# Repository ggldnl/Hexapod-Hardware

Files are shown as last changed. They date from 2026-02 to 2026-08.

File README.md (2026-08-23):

# Hexapod Hardware

<div align="center">
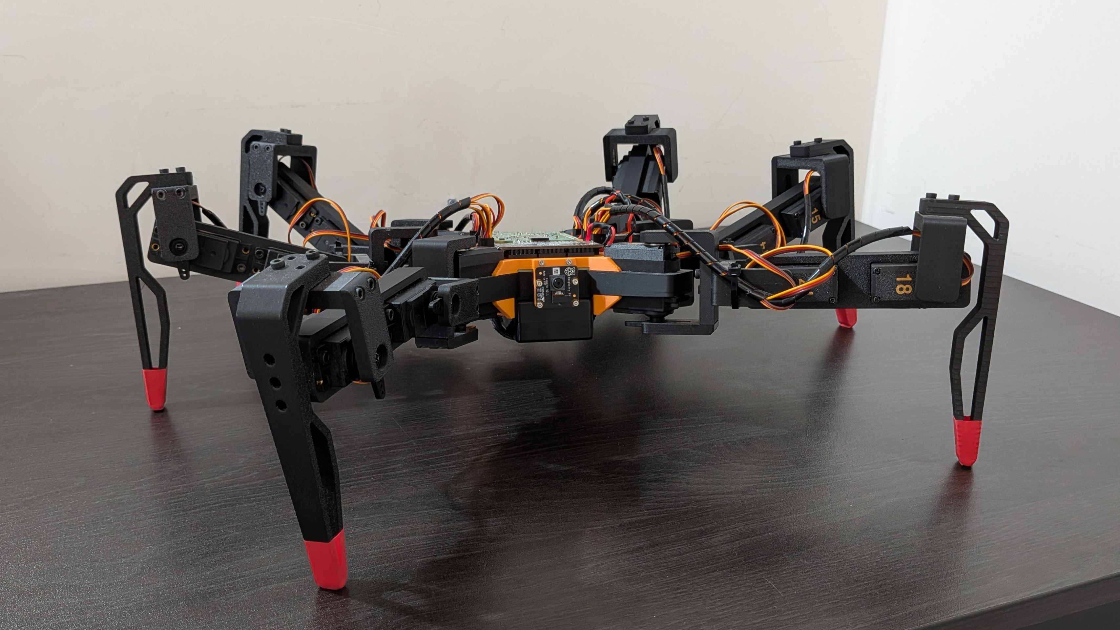
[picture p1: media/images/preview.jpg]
Preview
    
</div>

This repository contains the 3D-printed parts, BOM and assembly guide to replicate my hexapod robot. 

For a complete overview of the project, refer to the [main Hexapod repository](https://github.com/ggldnl/Hexapod). Additionally, you may want to check out the repositories containing the [Controller](https://github.com/ggldnl/Hexapod-Controller) and [Servo2040 firmware](https://github.com/ggldnl/Hexapod-Firmware).

## 🖼️ Render

A fusion 360 render can be found [here](https://a360.co/3SQCzxe).

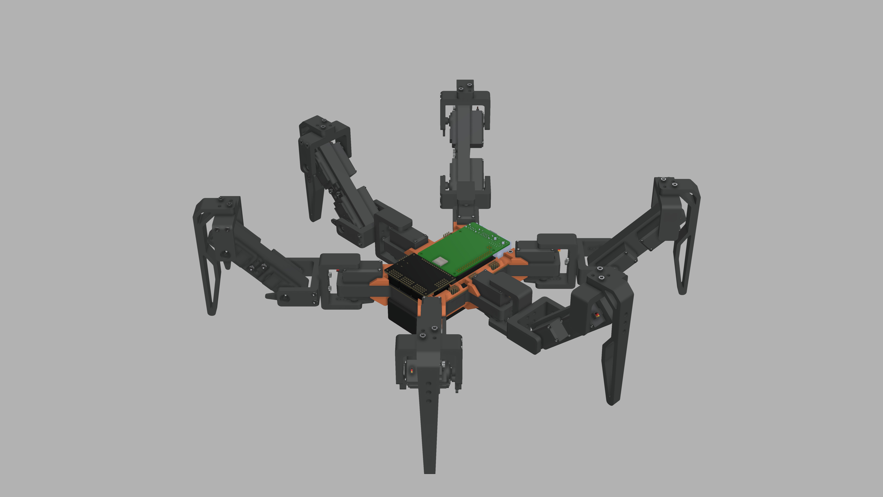
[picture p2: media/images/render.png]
Fusion 360 render (https://a360.co/3SQCzxe)


## 📋 Bill of Materials

Below is a summary of the components required to build the hexapod:

<div align="center">

| Category | Component | Quantity | Notes | Cost per part |
|---|---|---|---|---|
| Mechanical Components | 3D-printed parts | | 6 x `tibia`, 6 x `femur`, ... (refer to the [assembly instructions](#-assembly-instructions)) | |
| | M3 Screws | 92 |  | I bought an assorted 800pzs kit on Amazon for about 12€ and used different screw sizes from the kit. It's not important as long as they fit |
| | F686ZZ Bearings | 18 | You will need one for the back of each motor | About 10€ for 20pzs on Amazon |
| | M3 Heat set inserts | 92 |  | I bought a 150pzs kit on Amazon for about 10€ |
| Electronics | MG996/MG996R Servo | 18 | MG996R are cheaper but less powerful than MG996, they will do nevertheless | About 70€ on Aliexpress |
| | Servo2040 | 1 | An equivalent board can be used instead e.g. 2x Pololu Mini Maestro | About 28€ on the Pimoroni website |
| | Raspberry Pi 5 | 1 | Other versions can be used | About 100€ on Amazon |
| | 7.4V 2S LiPo Battery | 1 | They are often sold in pairs, so I ended up buying two of them for 50€ | About 25€ on Amazon |
| | 8A UBEC | 2 | You will need two of them, one for the servos and one for the electronics. I used [these ones](https://it.aliexpress.com/item/1005007467083035.html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): they have two channels with selectable input voltage and a power button. The `battery_mount` has two slots to hold this kind of UBECs. If you use a different model, you will need to redesign the part | About 20€ each on Aliexpress |

</div>

Approximate total cost: around 280€.

The prices listed in this BOM reflect the costs at the time of purchase and may no longer be accurate. This BOM is provided for reference only and should not be considered a precise cost estimate.

All above components are mandatory. There are two supported assembly paths, depending on whether you choose to use a [custom PCB I designed](https://github.com/ggldnl/Hexapod-PCB) or not.

1. With custom PCB

    Using the custom PCB slightly increases cost (about 60-70€ more) but simplifies the build, keeps the body slim, acts as a rigid base plate and saves you from having to deal with manual wiring. Refer to the [Hexapod PCB repository](https://github.com/ggldnl/Hexapod-PCB) for more information.

    The PCB is totally optional and you can skip it if you want to save a few bucks, but I highly recommend it.

2. Without custom PCB

    If the PCB is not used, the electronics can still be assembled, but with some compromises and additional parts. You will need to:

    - print the adapter plate `electronics_mount.stl` to mount the Servo2040 and Raspberry Pi. The result will be bulkier and with wires all over the place;
    - buy wire extenders as the rear legs are too far from the Servo2040;
    - buy M2 heat-set inserts and M2 screws (Servo2040 mounting holes are 2.7 mm);

    Once you have the necessary, add the M2 heat set inserts to the smaller holes in the `electronics_mount.stl`, secure the two boards and connect them according to [this guide](https://github.com/ggldnl/Hexapod-Firmware)

## 🖨️ 3D Printing Profile

Print profiles and STL files for the robot parts are [hosted on MakerWorld](https://makerworld.com/models/2655972-hexapod).

Make sure to follow the recommended print settings for optimal strength and fitment
Don't forget to boost the project!

## 🔨 Assembly Instructions

Each step below includes a short video.

1. Servos require a minor modification: replace the bottom section of the plastic housing with the custom 3D-printed part designed to hold an F686ZZ bearing, `servo_mod.stl`. This modification is fully reversible. I also added a small piece of kapton tape between the bearing and the circuit for good measure. You can reuse the same screws to secure the 3D-printed part in place. 

    <table>
        <tr>
            <td>
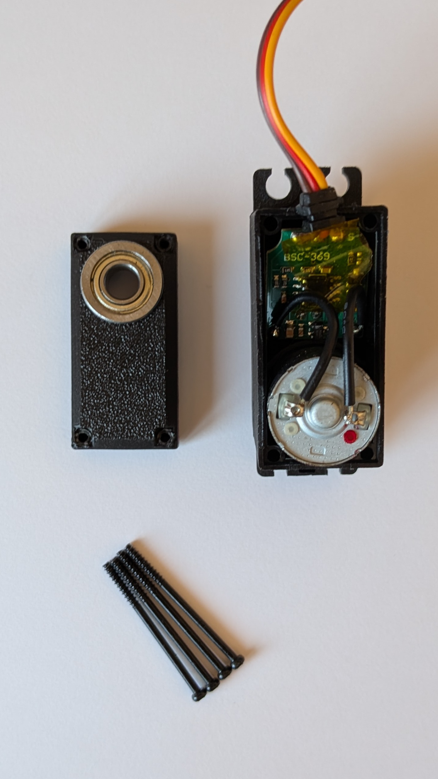
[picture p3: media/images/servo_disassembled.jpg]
Servo disassembled
                
            </td>
            <td>
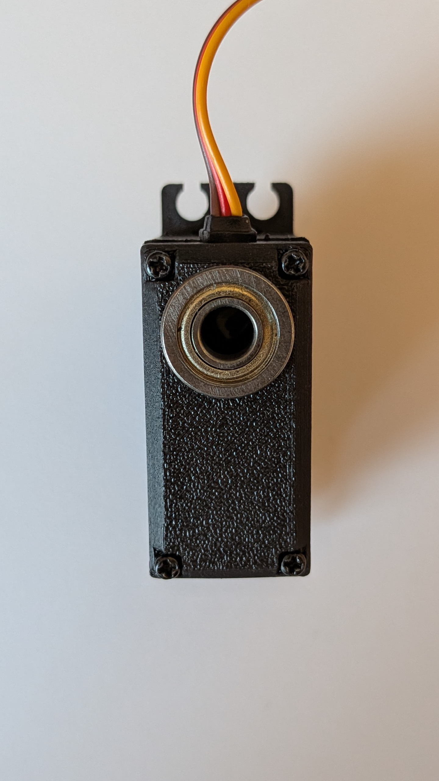
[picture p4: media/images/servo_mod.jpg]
Servo mod
                
            </td>
        </tr>
    </table>

2. Add heat set inserts to the 3D-printed parts. In some places I modeled 4 holes for the heat set inserts (servo hubs and brackets), but then only used 2. I didn't encounter any problems.

    <video src="https://github.com/user-attachments/assets/342bcc59-8d65-4aa1-9488-e9e4fd77accb"></video>

3. Now the legs. You will have to build 6 of them.

    <video src="https://github.com/user-attachments/assets/05f1056e-435a-43d8-accc-99606f1da784"></video>

4. Connect all the legs to the base.

    <video src="https://github.com/user-attachments/assets/e5f85936-af69-40fa-94dd-71543b65fb09"></video>

5. Add the electronics. Top and bottom stiffeners are NOT optional: they prevent the base from flexing. Ensure they actually touch the servos. Higher infill could also help.

    <video src="https://github.com/user-attachments/assets/8699bbb7-0d47-4d19-a4cc-e40c626c33b0"></video>

    <table>
        <tr>
            <td>
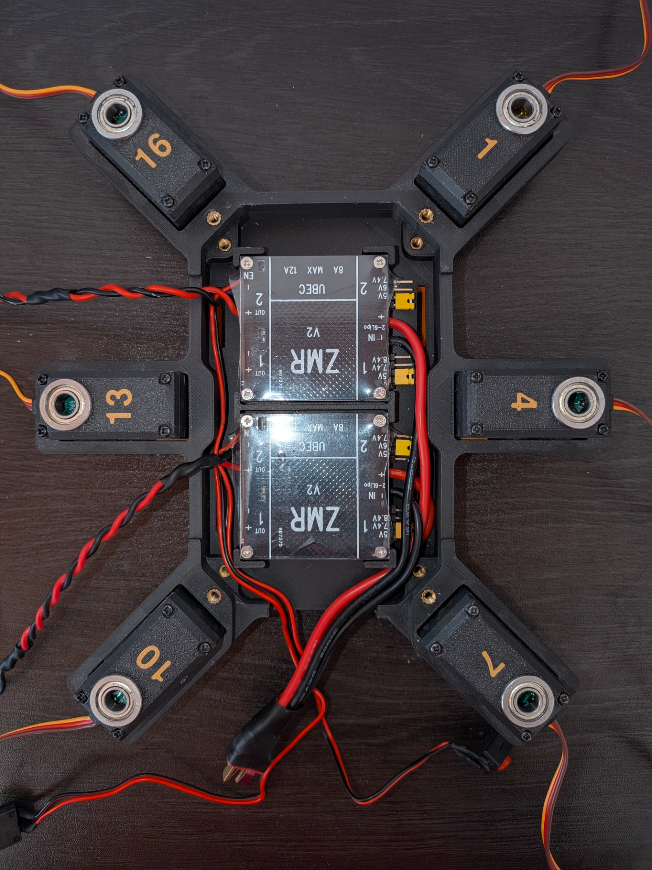
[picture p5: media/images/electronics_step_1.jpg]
Step 1
                
            </td>
            <td>
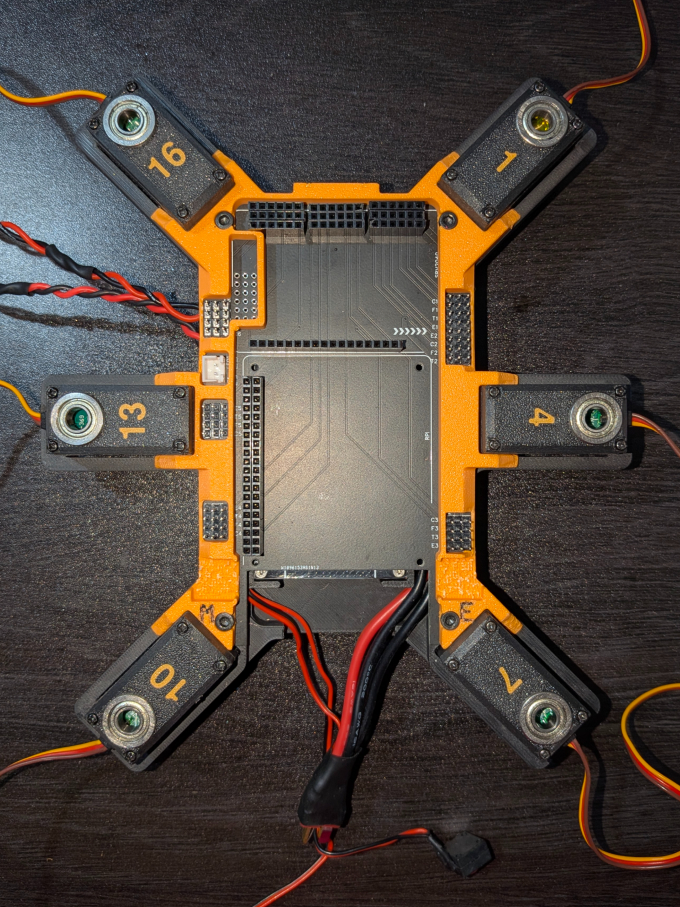
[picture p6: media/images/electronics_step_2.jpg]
Step 2
                
            </td>
            <td>
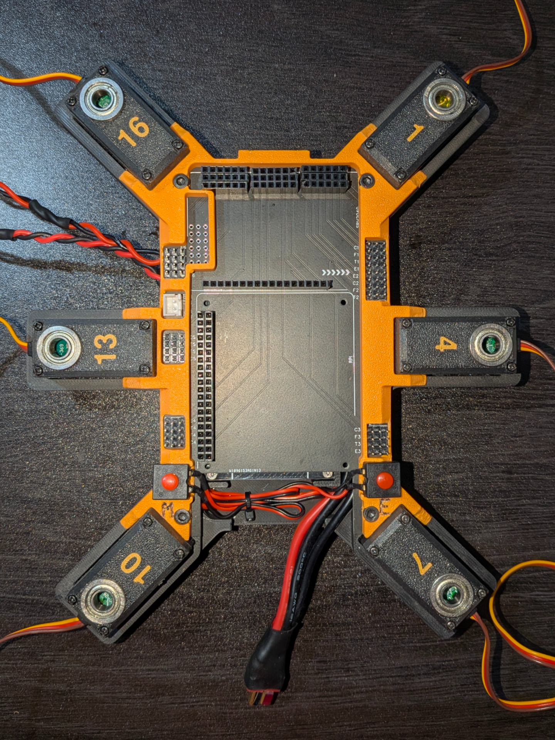
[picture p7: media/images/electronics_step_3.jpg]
Step 3
                
            </td>
        </tr>
    </table>

   - Optionally, cut off the cables on the unused channel on both UBECs to make some room. You can always solder them back if needed for a future project.
   - Use one UBEC to power the Raspberry Pi/Servo2040. If you use the custom PCB, it exposes a connector for that. Ensure the UBEC outputs 5V on the channel you are using, otherwise you will fry the boards. If you don't use the custom PCB, you can use the exposed pins on the Pi; the Servo2040 will get power from the UART connection.
   - Use the other UBEC to power the servos through the terminal block on the Servo2040. Servos can be powered at 6V (check their datasheet just in case). Again, make sure you select the correct voltage on the channel you use.
   - Solder together the inputs of the two UBECs.

6. Power the robot.

## 📝 Notes

1. All the legs use the same basic components (`CAD/stl/parts`): `femur.stl`, `tibia.stl`, 3 x `bracket_A.stl` and 3 x `bracket_B.stl`.
2. You will need 12 x `servo_mod.stl`, one for each servo. The mod is fully reversible. 
3. Files in the `CAD/stl/hardware` folder (`MG996.stl`, `battery.stl`, `electronics.stl`, ...) are used in the URDF for simulation, you don't need to print them. Refer to the [assembly instructions](#-assembly-instructions).
4. If you don't want to use the custom PCB, you will need to print the `CAD/stl/parts/electronics_mount.stl` and buy some more components (M2 heat set inserts and screws). Refer to [this section ](#without-custom-pcb).
5. You can edit the printed parts to your likings. STEP files are in the `CAD/step/parts` folder.

## 🤝 Contribution

Feel free to raise issues or contribute improvements to this repository. For further information about the project, check out the [main Hexapod repository](https://github.com/ggldnl/Hexapod). Give a ⭐️ to this project if you liked the content.

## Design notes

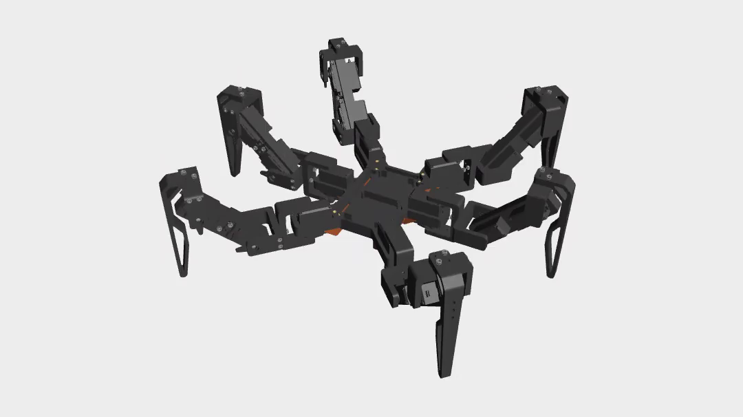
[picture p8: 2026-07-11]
media/thumbnails/electronics_to_base.png

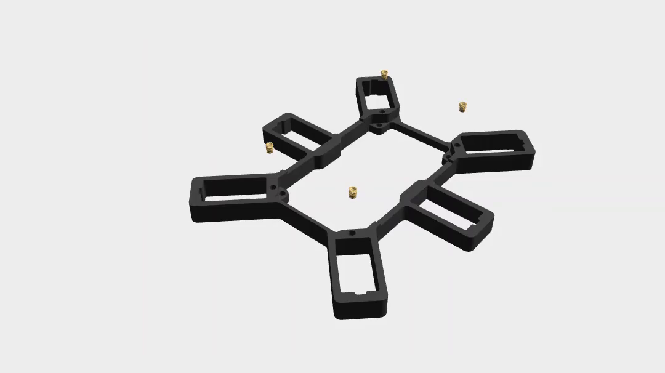
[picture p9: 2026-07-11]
media/thumbnails/heat_set_inserts.png

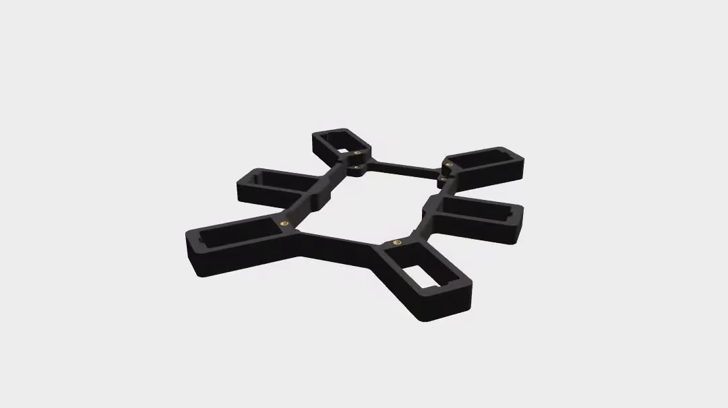
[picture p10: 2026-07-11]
media/thumbnails/legs_to_base.png

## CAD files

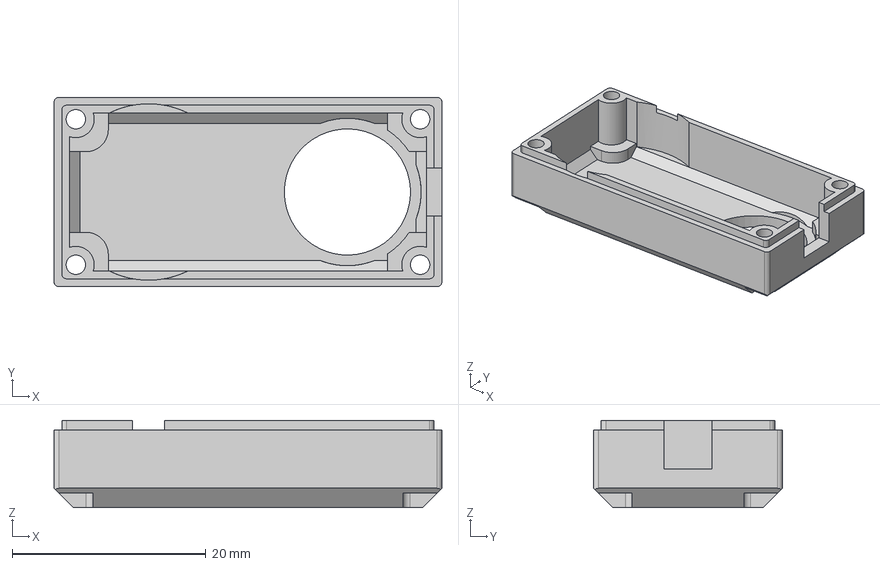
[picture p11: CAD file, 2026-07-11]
CAD/step/parts/servo_mod.step
40.0 x 19.5 x 9.00 mm

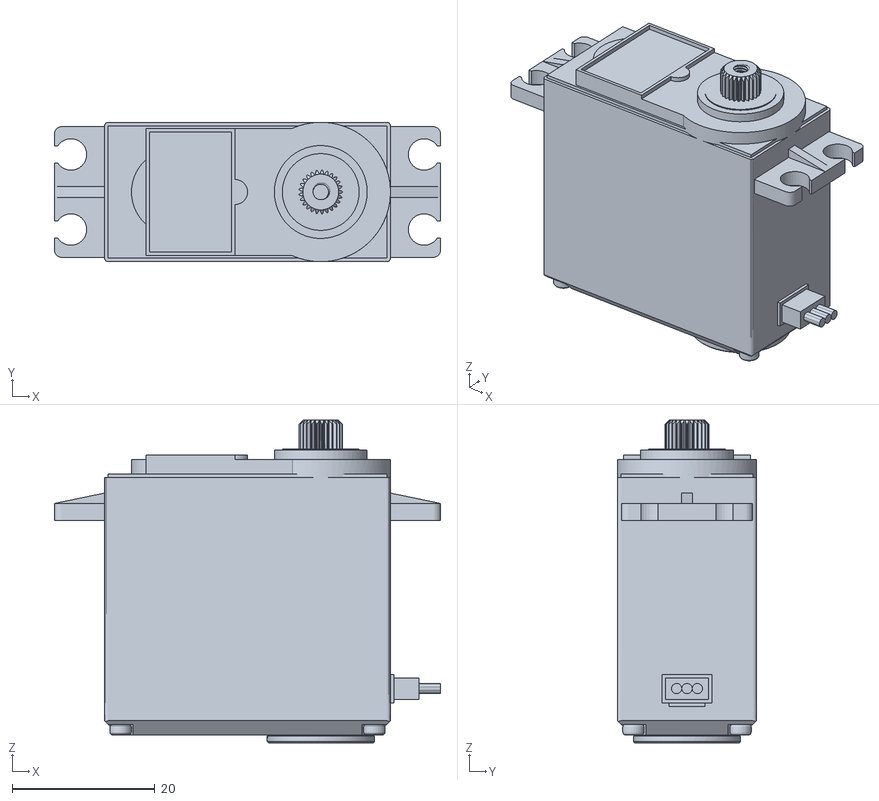
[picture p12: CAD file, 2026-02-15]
CAD/stl/hardware/MG996R.stl
54.0 x 19.5 x 45.1

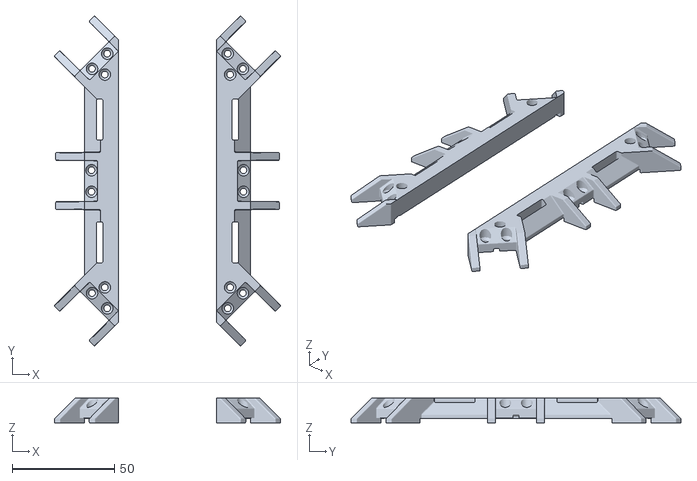
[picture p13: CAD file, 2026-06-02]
CAD/stl/parts/bottom_stiffeners.stl
110.5 x 161.2 x 12.0

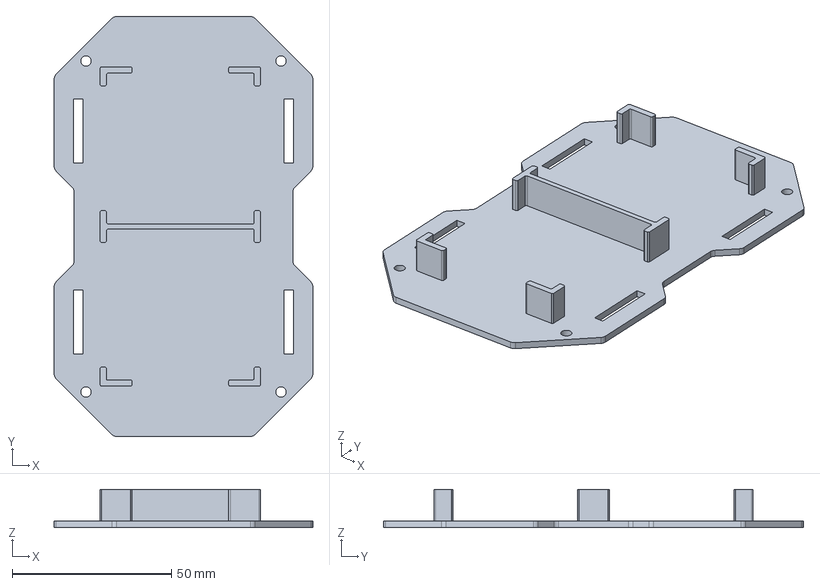
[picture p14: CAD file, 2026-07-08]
CAD/step/parts/battery_mount.step
81.3 x 132.0 x 12.0 mm

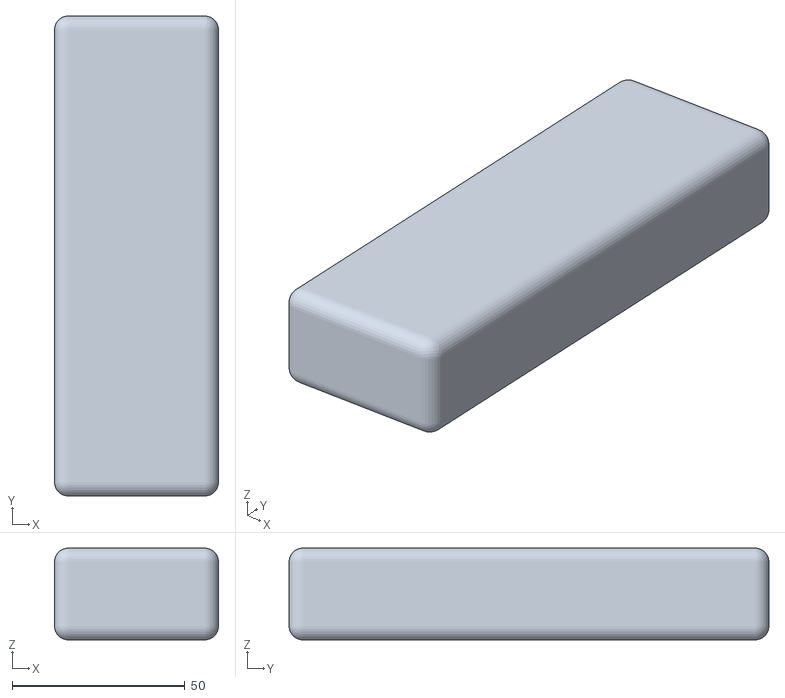
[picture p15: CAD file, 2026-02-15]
CAD/stl/hardware/battery.stl
47.5 x 139.0 x 26.6

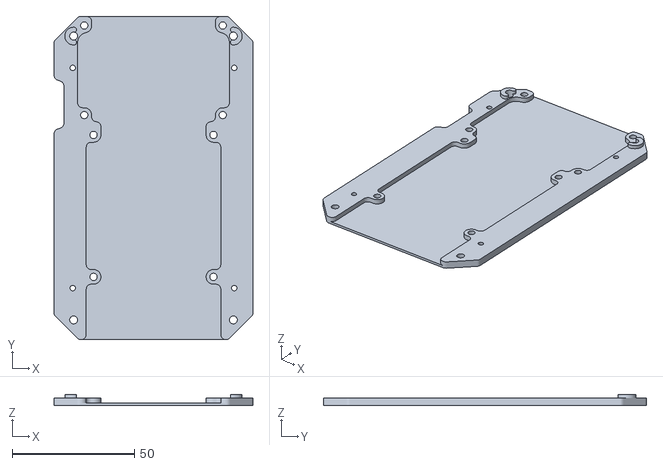
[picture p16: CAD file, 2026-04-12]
CAD/stl/parts/electronics_mount.stl
81.3 x 132.0 x 4.50

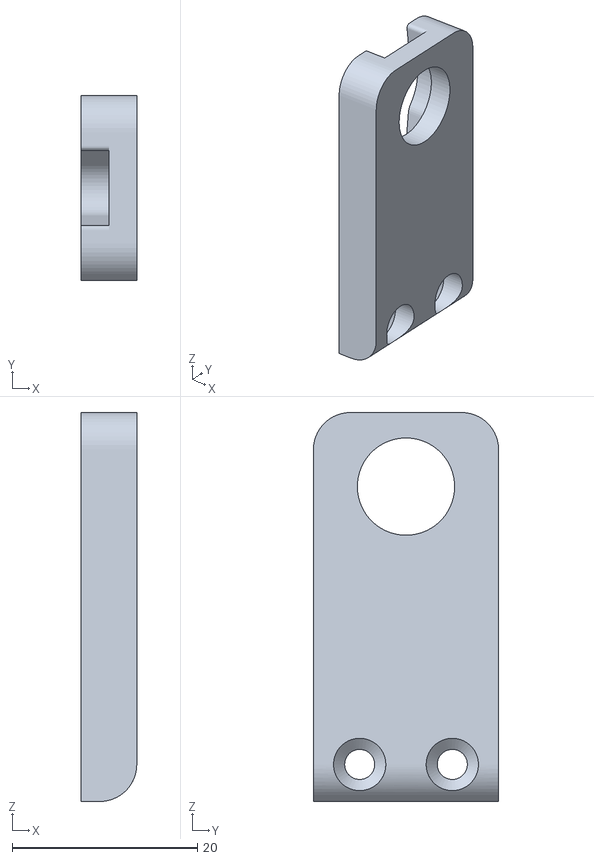
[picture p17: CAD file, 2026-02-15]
CAD/stl/parts/bracket_B.stl
6.00 x 20.0 x 42.0

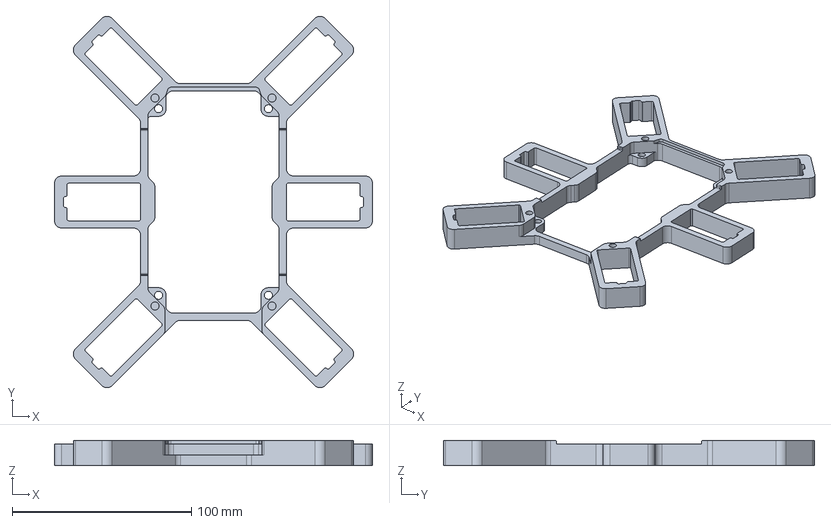
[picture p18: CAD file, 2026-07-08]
CAD/step/parts/base.step
177.3 x 207.1 x 14.0 mm

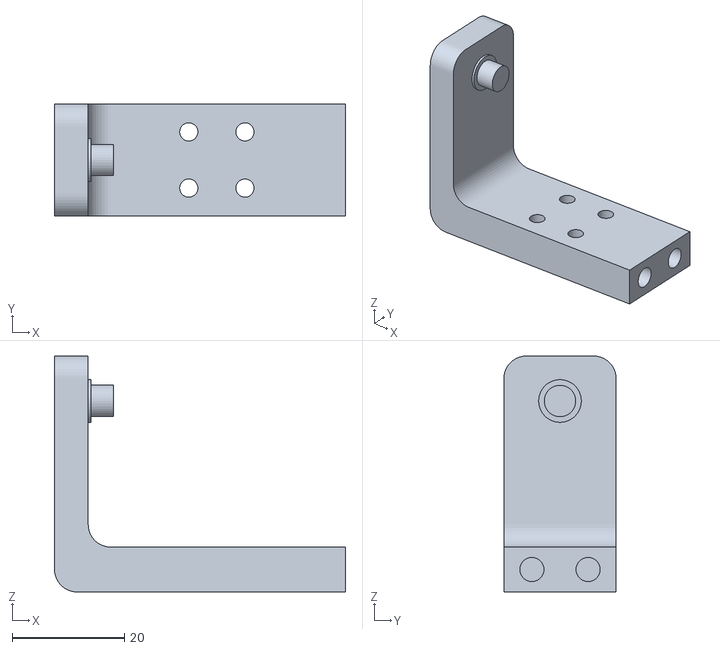
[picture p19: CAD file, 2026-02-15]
CAD/stl/parts/bracket_A.stl
51.8 x 20.0 x 42.0

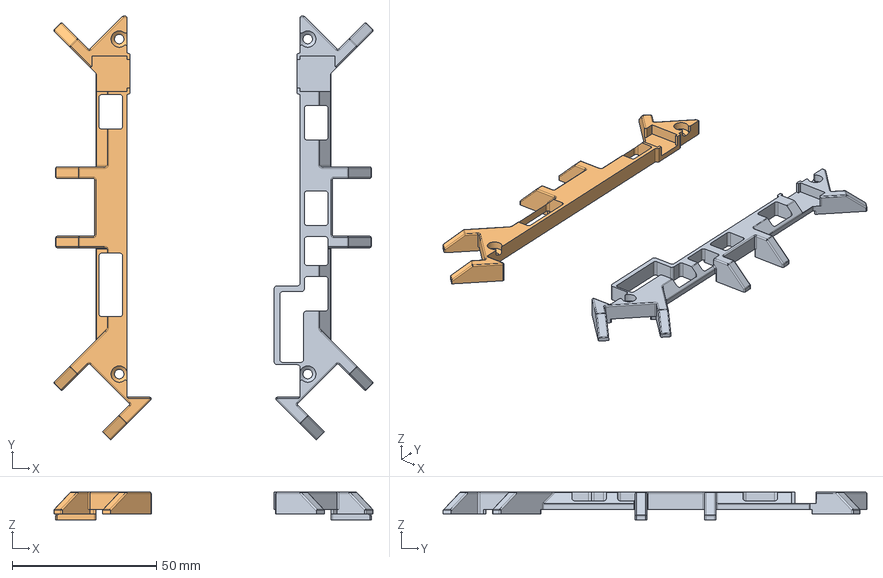
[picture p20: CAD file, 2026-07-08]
CAD/step/parts/top_stiffeners.step
110.5 x 146.8 x 9.60 mm

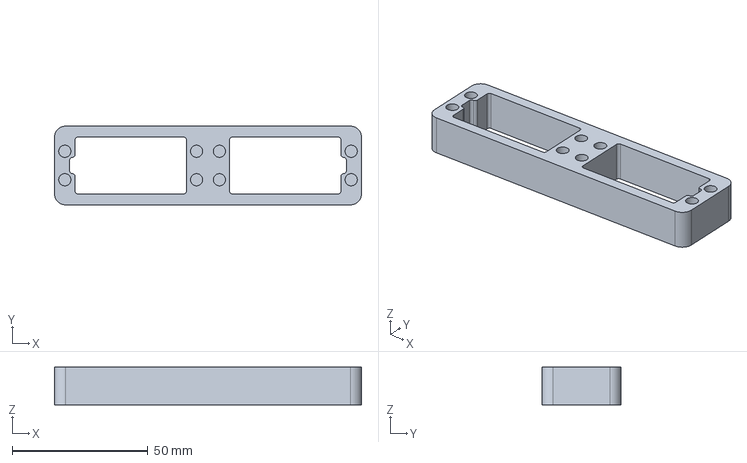
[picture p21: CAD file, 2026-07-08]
CAD/step/parts/femur.step
113.2 x 29.0 x 14.0 mm

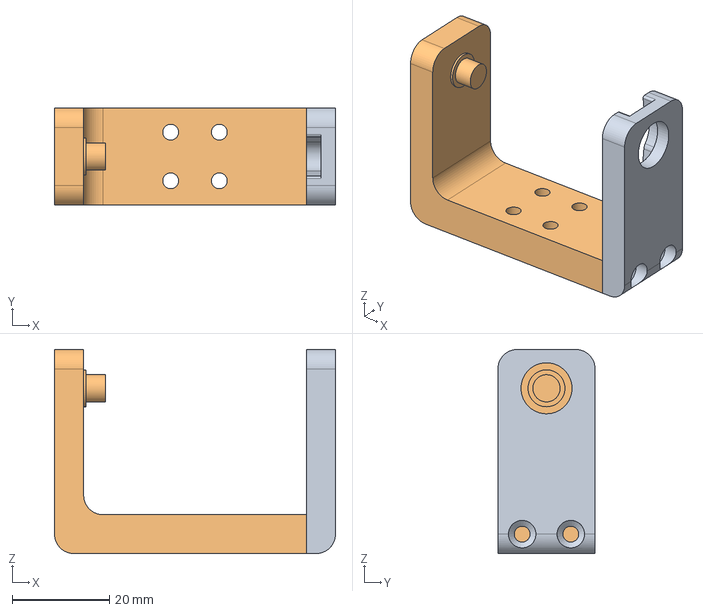
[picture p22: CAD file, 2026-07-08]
CAD/step/parts/motor_bracket.step
57.8 x 20.0 x 42.0 mm

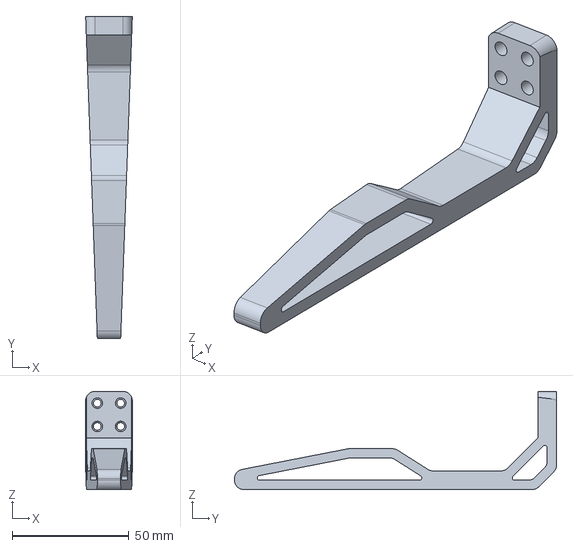
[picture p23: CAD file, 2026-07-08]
CAD/step/parts/tibia.step
20.0 x 137.8 x 42.0 mm

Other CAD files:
CAD/step/parts/bottom_stiffener.step
CAD/stl/parts/base.stl
CAD/stl/parts/battery_mount.stl
CAD/stl/parts/femur.stl
CAD/stl/parts/servo_mod.stl
CAD/stl/parts/tibia.stl
CAD/stl/parts/top_stiffeners.stl

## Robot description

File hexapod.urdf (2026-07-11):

<?xml version='1.0' encoding='utf-8'?>
<robot name="Hexapod">

    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

    <link name="base">
        <inertial>
            <origin xyz="-4.567197330417133e-06 0.0014207813889969261 0.00658135692503016" rpy="0.0 0.0 0.0" />
            <mass value="0.07235996288634414" />
            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
        </inertial>
        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
    </link>

    <link name="battery">
        <inertial>
            <origin xyz="-1.8325864203916354e-09 -0.0019999975978255338 0.013299996384758385" rpy="0.0 -0.0 0.0" />
            <mass value="0.18315250842415606" />
            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
        </inertial>
        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
    </link>
    
    <link name="electronics">
        <inertial>
            <origin xyz="-0.03014211279323742 -0.060922952696511316 -0.006406493150595711" rpy="0.0 -0.0 -5.58101059878747e-104" />
            <mass value="0.07571894822352634" />
            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
        </inertial>
        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
    </link>
    
    <link name="battery_mount">
        <inertial>
            <origin xyz="0.00021369715366641008 0.06600122552697489 0.00035714174971326787" rpy="0.0 -0.0 -5.58101059878747e-104" />
            <mass value="0.1649336841152355" />
            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
        </inertial>
        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
    </link>

    <link name="top_stiffeners">
        <inertial>
            <origin xyz="-0.03355588058631941 -0.05570358348592372 -0.0023873886142182243" rpy="0.0 -0.0 0.0" />
            <mass value="0.01808559434559243" />
            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
        </inertial>
        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
    </link>

    <link name="bottom_stiffeners">
        <inertial>
            <origin xyz="-0.030635001832586425 -0.0519999971308711 0.0042514629347305015" rpy="0.0 -0.0 0.0" />
            <mass value="0.04994655381225562" />
            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
        </inertial>
        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
    </link>

    <joint name="base_electronics" type="fixed">
        <origin xyz="-0.03263500183258655 0.057999997597825405 0.013999996384758396" rpy="3.1415926535897927 -1.883898413669496e-21 -3.14159265358979" />
        <parent link="base" />
        <child link="electronics" />
    </joint>

    <joint name="base_battery_mount" type="fixed">
        <origin xyz="-1.8325866024682113e-09 0.06599999759782552 -3.6152415994195054e-09" rpy="-3.1415926535897927 1.883898413669496e-21 3.066991105526992e-15" />
        <parent link="base" />
        <child link="battery_mount" />
    </joint>

    <joint name="battery_mount_battery" type="fixed">
        <origin xyz="0.0 0.06600000000000002 0.0020000000000000018" rpy="1.4836778140138092e-67 -3.76158192263132e-37 3.141592653589793" />
        <parent link="battery_mount" />
        <child link="battery" />
    </joint>

    <joint name="electronics_top_stiffeners" type="fixed">
        <origin xyz="0.0 0.0 -0.0012000000000000012" rpy="2.7755575615628914e-17 -3.76158192263132e-37 -3.9442911284505303e-31" />
        <parent link="electronics" />
        <child link="top_stiffeners" />
    </joint>

    <joint name="battery_mount_bottom_stiffeners" type="fixed">
        <origin xyz="-0.030634999999999996 0.013999999999999986 0.0020000000000000018" rpy="1.4836778140138092e-67 -3.76158192263132e-37 3.141592653589793" />
        <parent link="battery_mount" />
        <child link="bottom_stiffeners" />
    </joint>

    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

    <link name="leg_1_coxa_motor">
        <inertial>
            <origin xyz="0.013574471662495436 0.020999093948920588 0.008369892907608513" rpy="0.0 -0.0 0.0" />
            <mass value="0.029139949883713843" />
            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
        </inertial>
        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
    </link>
    <link name="leg_1_coxa_bracket_B">
        <inertial>
            <origin xyz="-0.003105251669849143 0.014525191609803123 -0.0074541224383952095" rpy="5.691615141457044e-61 -0.0 0.0" />
            <mass value="0.004130529991365324" />
            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
        </inertial>
        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
    </link>
    <link name="leg_1_coxa_bracket_A">
        <inertial>
            <origin xyz="-0.015926416210366803 -0.015926407039013685 -0.010950415401159198" rpy="0.0 -0.0 0.0" />
            <mass value="0.01302030082235085" />
            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
        </inertial>
        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
    </link>
    <link name="leg_1_femur_bracket_A">
        <inertial>
            <origin xyz="-0.012675760983264742 -0.003554678519033221 0.005000003203434631" rpy="0.0 -0.0 0.0" />
            <mass value="0.01302030082235085" />
            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
        </inertial>
        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
    </link>
    <link name="leg_1_femur_bracket_B">
        <inertial>
            <origin xyz="-0.0049999967965269135 -0.013185405881645487 0.008793910918232131" rpy="0.0 -0.0 0.0" />
            <mass value="0.004130529991365324" />
            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
        </inertial>
        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
    </link>
    <link name="leg_1_femur_motor">
        <inertial>
            <origin xyz="5.4061232124258395e-09 -0.0231178146864527 -0.008979636323357543" rpy="4.337878534446334e-75 -0.0 0.0" />
            <mass value="0.029139949883713843" />
            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
        </inertial>
        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
    </link>
    <link name="leg_1_femur">
        <inertial>
            <origin xyz="-0.04233946112690463 -0.032331021486653955 -0.005249996796564785" rpy="0.0 7.006492321624085e-46 1.2066609121497597e-89" />
            <mass value="0.021802151943504742" />
            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
        </inertial>
        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
    </link>
    <link name="leg_1_tibia_motor">
        <inertial>
            <origin xyz="0.011368372072919223 -0.023205191063109327 0.005249998999252793" rpy="0.0 -0.0 -1.9481407417666057e-90" />
            <mass value="0.029139949883713843" />
            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
        </inertial>
        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
    </link>
    <link name="leg_1_tibia_bracket_A">
        <inertial>
            <origin xyz="-0.008183294094499942 -0.023669531630267856 3.203435771093055e-09" rpy="0.0 -0.0 -5.001342253538129e-90" />
            <mass value="0.01302030082235085" />
            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
        </inertial>
        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
    </link>
    <link name="leg_1_tibia_bracket_B">
        <inertial>
            <origin xyz="-0.004999996796602597 0.008793918304699026 -0.013185403268111866" rpy="1.5241149863310267e-61 8.758115402030107e-47 0.0" />
            <mass value="0.004130529991365324" />
            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
        </inertial>
        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
    </link>
    <link name="leg_1_tibia">
        <inertial>
            <origin xyz="0.026965073129646255 0.03403614230100331 -0.026581936859366603" rpy="0.0 -3.503246160812043e-46 0.0" />
            <mass value="0.02243468417663065" />
            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
        </inertial>
        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
    </link>
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

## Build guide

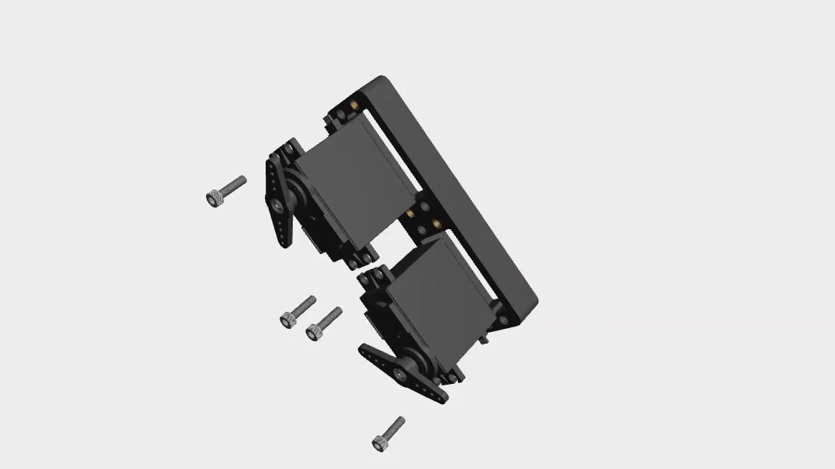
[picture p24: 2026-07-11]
media/thumbnails/leg_assembly.png

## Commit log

2024-12-26 Updated CAD model
    [base.stl, bottom_plate.stl, hardware_layer_1.stl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]
2024-12-27 Renamed electronics mounts
    [electronics_layer_1.stl, electronics_layer_2.stl]
2024-12-27 Moved URDFs to this repository
    [hexapod.urdf, leg_left.urdf, leg_right.urdf]
2024-12-27 Updated paths to stl objects
    [leg_left.urdf, leg_right.urdf]
2024-12-28 Color set to gray for better visualization
    [hexapod.urdf]
2025-01-03 Now we have two URDF: one with all the details and the other one with only the bare minimum
    [hexapod_bare_minimum.urdf]
2025-01-28 Updated tibia
    [tibia_left.stl, tibia_right.stl]
2025-02-10 Hardware update
    [MG996.stl, MG996R.stl, base.stl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]
2025-02-10 Fixed typo
    [hexapod.urdf, hexapod_bare_metal.urdf, leg_right.urdf]
2025-02-11 Base -> Body in a random comment idk
    [hexapod.urdf]
2026-01-21 New hexapod version
    [MG996R.stl, base.stl, bottom_plate.stl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]
2026-01-21 Removed old URDFs
    [hexapod_bare_metal.urdf, leg_left.urdf, leg_right.urdf]
2026-01-21 Slight offset on leg 4 tibia joint
    [hexapod.urdf]
2026-01-23 Regenerated URDF to use actual parts
    [adapter_plate_a.stl, adapter_plate_b.stl, coxa.stl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]
2026-01-23 Added a note on adapter plate
2026-01-23 Incorrect mesh for leg 6 coxa
    [hexapod.urdf]
2026-01-24 Corrupted joint leg 3
    [hexapod.urdf]
2026-01-24 Renamed joints
    [hexapod.urdf]
2026-01-24 Typo in joint 6 coxa name
    [hexapod.urdf]
2026-01-26 Added electronics and battery
    [hexapod.urdf, hexapod_skeleton.urdf]
2026-01-26 Added melectronics and battery meshes
    [battery.stl]
2026-01-26 Updated base orientation
    [hexapod.urdf]
2026-01-26 Updated base orientation, again
    [hexapod.urdf]
2026-01-26 Rotated base frame again
    [hexapod.urdf]
2026-01-27 Merged the two halves of the adapter plate
    [adapter_plate.stl, adapter_plate_a.stl, adapter_plate_b.stl]
2026-01-28 slightly changed tibia and base
    [base.stl, tibia.stl]
2026-01-30 Updated base
    [base.stl]
2026-02-10 Fixed old mesh path
    [hexapod.urdf]
2026-02-15 Improved structure and better URDF for physics simulation
    [MG996R.stl, adapter_plate.stl, base.stl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]
2026-03-03 Added electronics
    [base_cover.stl, battery_mount.stl, camera.stl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]
2026-03-03 Split printed parts and hardware into two separate folders
    [MG996R.stl, base.stl, battery.stl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]
2026-03-03 Added material to new bodies
    [hexapod.urdf]
2026-03-14 Fix link to Servo2040 firmware repository
2026-03-23 Fixed weird bug with inertia coefficients for leg 2 being off
    [hexapod.urdf]
2026-04-12 Removed camera -> now optional
    [camera.stl, camera_mount.stl, hexapod.urdf]
2026-04-12 Added missing files
    [electronics_mount.stl, servo_bottom_housing.stl]
2026-04-12 Added button mounts
    [electronics_UBEC_button_mount.stl, motors_UBEC_button_mount.stl]
2026-05-24 Added stiffeners
    [bottom_stiffener_left.stl, bottom_stiffener_right.stl, top_stiffener_camera_mount.stl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]
